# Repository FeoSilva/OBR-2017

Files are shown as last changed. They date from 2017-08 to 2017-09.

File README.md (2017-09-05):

# OBR 2017 - Equipe Robonáticos
Robô autônomo (Paulo) participante da Olimpíada Brasileira de Robótica.
<br><br>
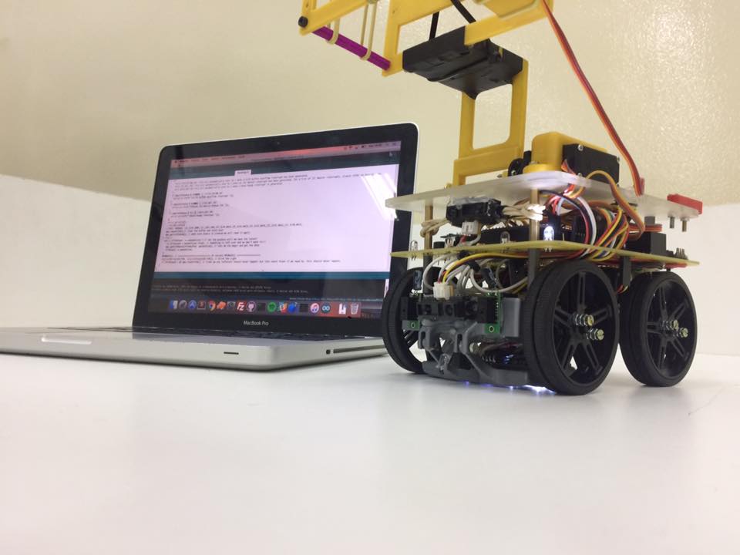
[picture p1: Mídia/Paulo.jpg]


Competições:
- Etapa Regional (FEI I) - 11/08/2017 - 1° lugar com 490 pts na somatória
- Etapa Estadual (FEI) - 09/09/2017

Resultados da Etapa Regional:
http://www.sistemaolimpo.org/regionais/results.php?eventID=3

<b>Divisões</b>
- Mecânica (12 versões do robô feitas para etapa regional utilizando o SolidWorks)
- Eletrônica (3 versões da Placa Principal para etapa regional utilizando o Eagle)
- Programação (45 versões do código até o final - Código em C++)

<b>Componentes do robô:</b><br>
<a href="https://store.arduino.cc/usa/arduino-mega-2560-rev3">- 1x Arduino Mega</a><br>
<a href="https://www.pololu.com/product/3045">- 4x 298:1 Micro Metal Gearmotor HPCB 12V</a><br>
<a href="https://www.pololu.com/product/713/resources">- 1x TB6612FNG (Controlador dos Motores);</a><br>
<a href="https://www.pololu.com/product/1425">- 8x Rodas Pololu 70x8mm</a><br>
<a href="https://www.filipeflop.com/produto/acelerometro-e-giroscopio-3-eixos-6-dof-mpu-6050/">- 1x MPU6050 - Acelerômetro e Giroscópio</a><br>
<a href="https://www.pololu.com/product/1134">- 4x Sharp Sensor Digital 2-10 cm</a><br>
<a href="https://www.pololu.com/product/2464">- 2x Sharp Sensor Analógico 4-30 cm</a><br>
<a href="https://www.pololu.com/product/960">- 1x QTR Sensor Array Analógico</a><br>
<a href="http://www.usinainfo.com.br/sensores-para-arduino/sensor-de-cor-para-arduino-tcs230-2810.html">- 2x TSC 230 - Sensor de Cor</a><br>
<a href="http://produto.mercadolivre.com.br/MLB-876602966-bateria-lipo-turnigy-2200mah-3s-111v-20c-_JM">- 1x Bateria de Li-po 11.1V 3S</a><br>
<a href="https://www.filipeflop.com/produto/servo-towerpro-mg995-metalico/">- 1x Servo MG995 15 kg.F.cm</a><br>
<a href="https://www.filipeflop.com/produto/micro-servo-9g-sg90-towerpro/">- 1x Micro servo SG90 Tower Pro</a>

<b>Fatores que serão melhorados/implementados para Etapa Estadual</b>
- Inclusão de encoder nos motores para aperfeiçoar as verificações e curvas do robô<br>
- Replanejamento dos sensores de distância para identificar as vítimas<br>
- Aperfeiçoamento da mecânica geral do robô para melhorar o centro de massa e diminuir sua altura<br>
- Aperfeiçoamento do mecanismo de recolher as vitímas<br>
- Implementação do algoritmo de cálculo percentual de proximidade de cor para detectar melhor a fita verde

<b>Integrantes:</b>
- Felipe Oliveira Silva (18 anos - Programação / Eletrônica);
- Antonio Pereira de Lima Neto (18 anos - Programação);
- Giovanna Ferreira Diodato (16 anos - Programação);
- Felipe de Souza Tiozo (17 anos - Mecânica / Eletrônica);

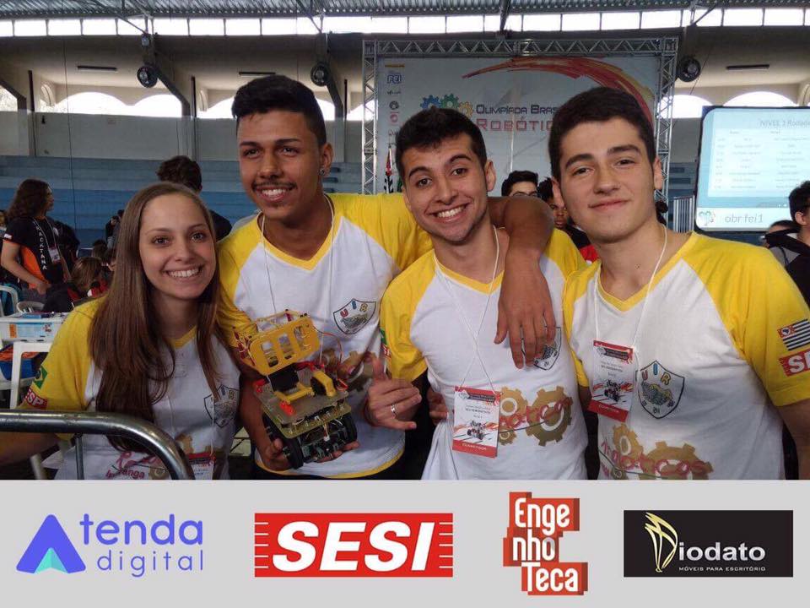
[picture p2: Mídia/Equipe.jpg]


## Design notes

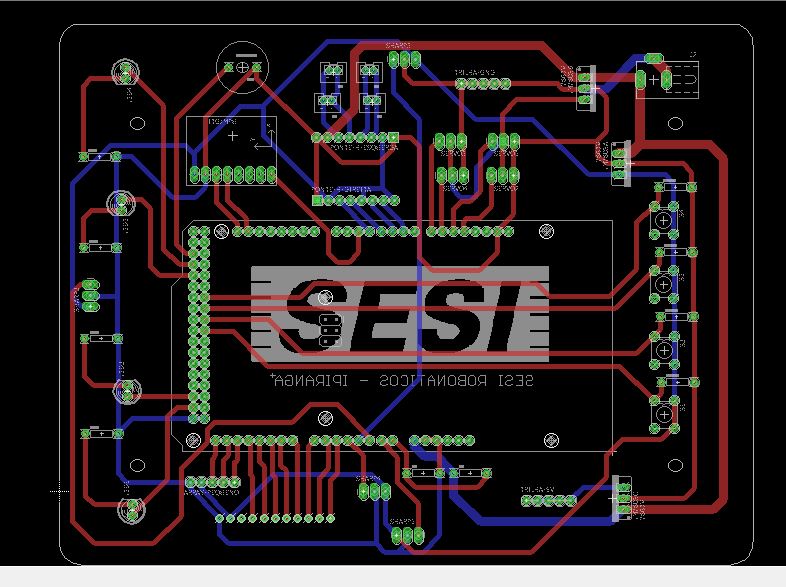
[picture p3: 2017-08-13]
Eletrônica/Paulo V2/placa.JPG

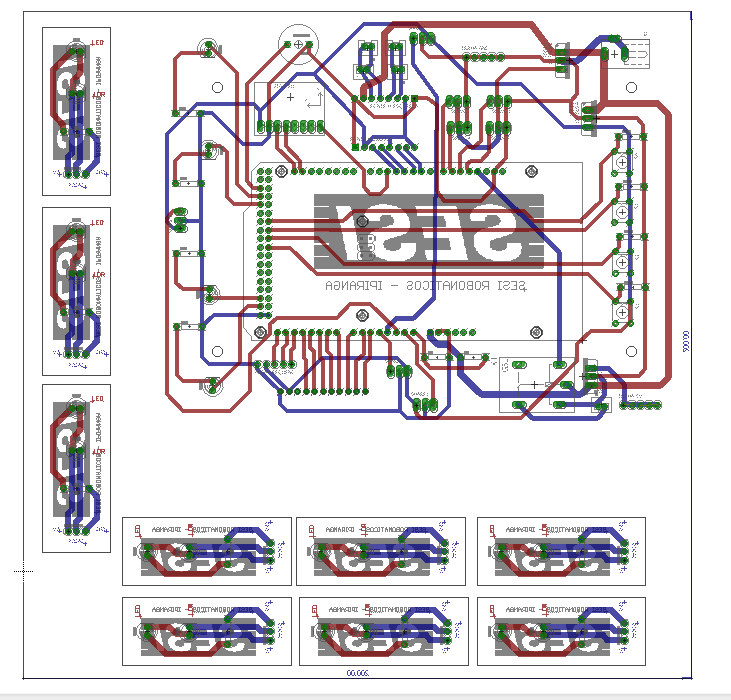
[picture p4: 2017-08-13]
Eletrônica/Placa Final/placa-final.PNG

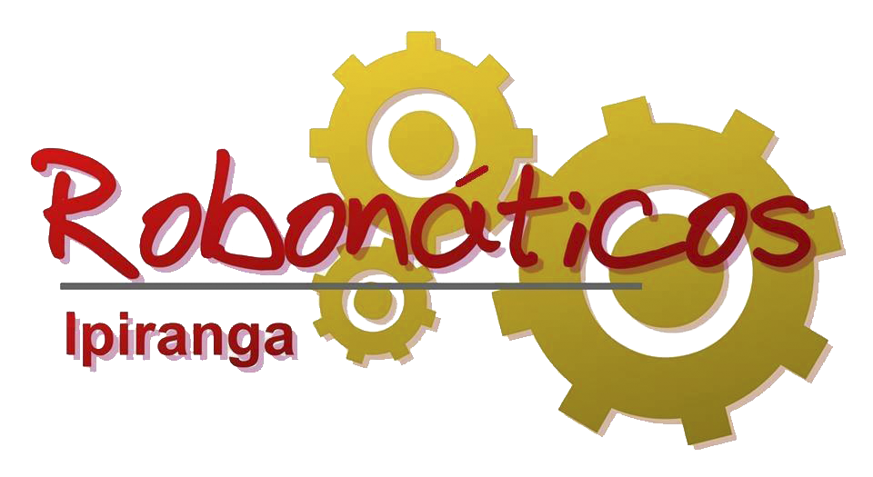
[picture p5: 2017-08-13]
Eletrônica/Placa LDR/robonaticos.png

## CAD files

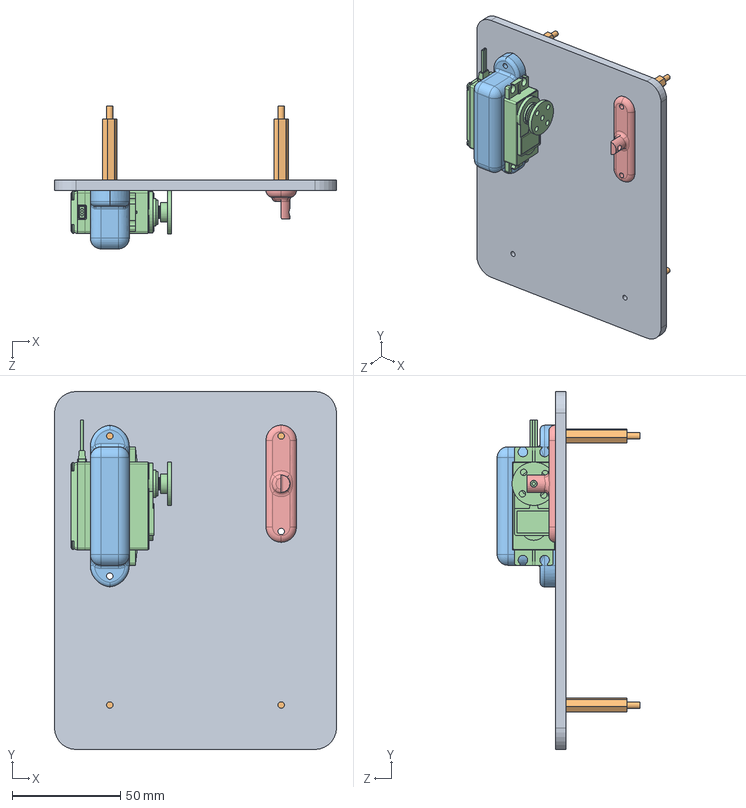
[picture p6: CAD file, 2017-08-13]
Mecânica/Paulo V12/Garra/Garra.SLDASM
130.0 x 165.0 x 65.8 mm
Chassi-Cima
Standoff-Nylon x 4
Suporte-Servo-MG
Servo-MG-995
Mancal

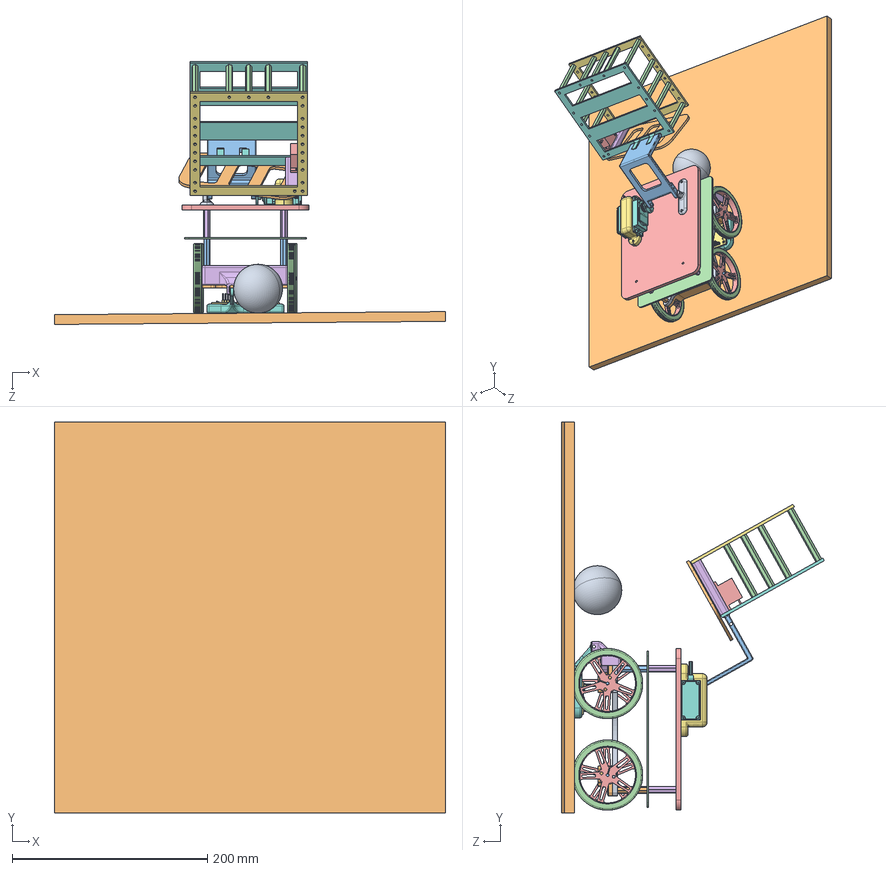
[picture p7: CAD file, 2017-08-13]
Mecânica/Paulo V12/Paulo-Montagem.SLDASM
400.1 x 400.0 x 269.0 mm
Chassi-Baixo
Suporte-Motor x 2
Pololu #2218 Micro Metal Gearmotor HP x 4
Borracha x 4
Roda x 4
Suporte-Trava-Array
Color_sensor x 2
Suporte-Array-Movel (1)
Standoff-Baixo-Maior x 2
Standoff-Baixo-Menor x 2
PCB
Chassi-Cima
Standoff-Nylon x 4
Suporte-Servo-MG
Servo-MG-995
Mancal
Piso
Mecanismo
Standoff-Garra x 12
Servo-9g
Suporte-Servo-Caixa
Base-Caixa
Tampa-Caixa
Vitima
Porta-Servo

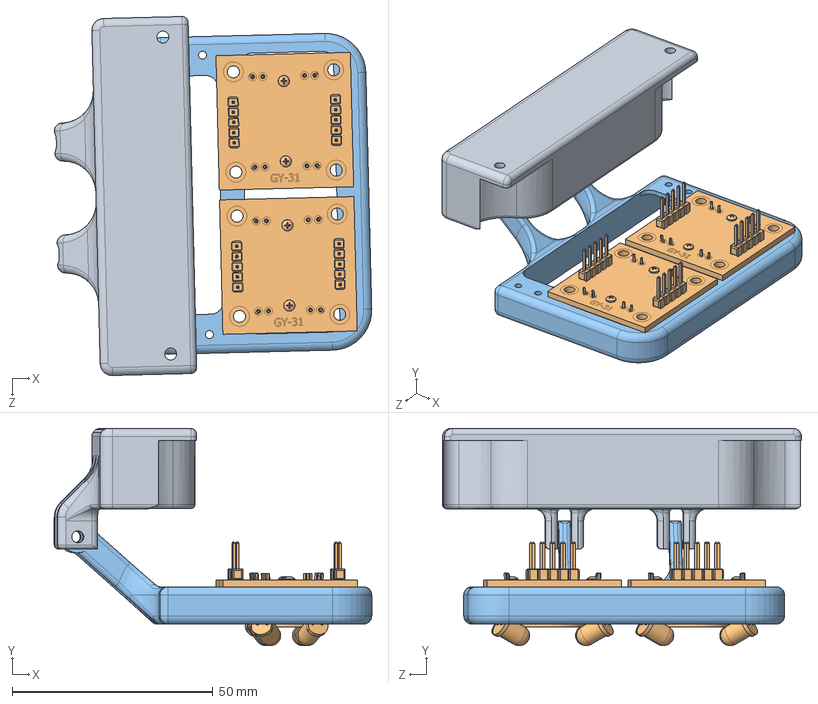
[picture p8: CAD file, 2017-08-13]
Mecânica/Paulo V12/Suporte-Array/Montagem-Suporte-Sensor.SLDASM
79.1 x 54.1 x 89.5 mm
Suporte-Trava-Array
Color_sensor x 2
Suporte-Array-Movel (1)

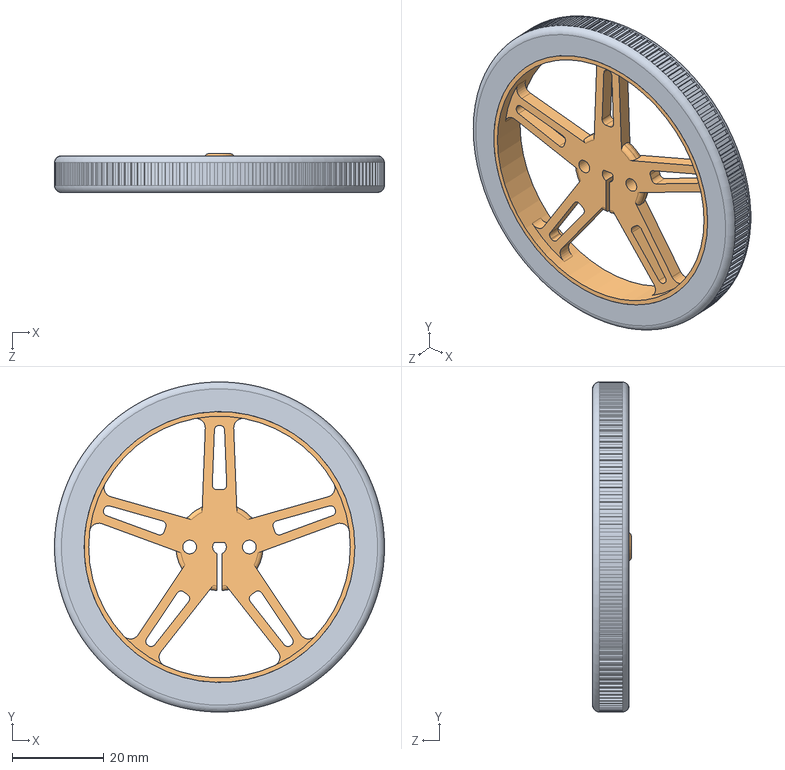
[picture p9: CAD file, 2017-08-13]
Mecânica/Paulo V12/Mobilidade/Pneu/Pneu.SLDASM
71.9 x 71.9 x 8.50 mm
Borracha
Roda

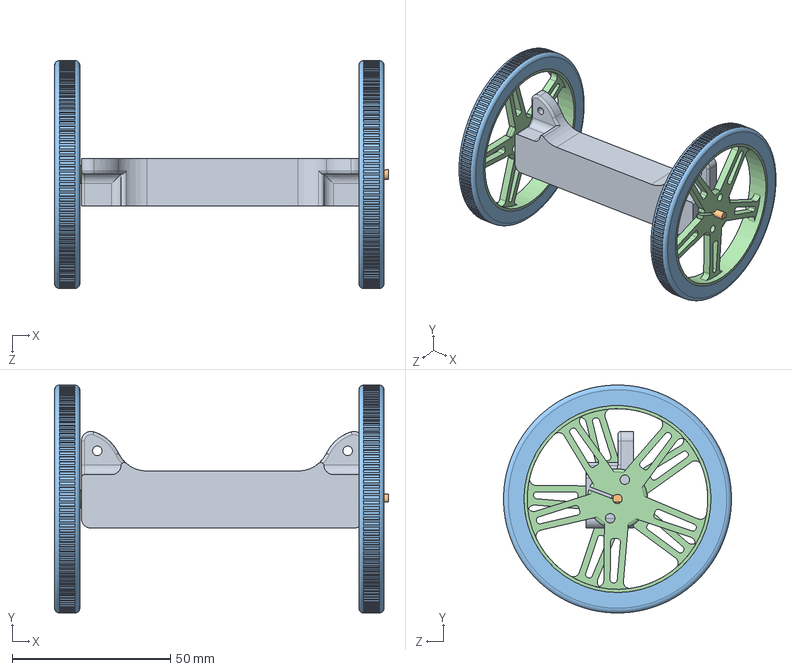
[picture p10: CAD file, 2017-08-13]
Mecânica/Paulo V12/Mobilidade/Motores-Suporte-Roda.SLDASM
105.4 x 71.9 x 71.9 mm
Suporte-Motor
Pololu #2218 Micro Metal Gearmotor HP x 2
Borracha x 2
Roda x 2

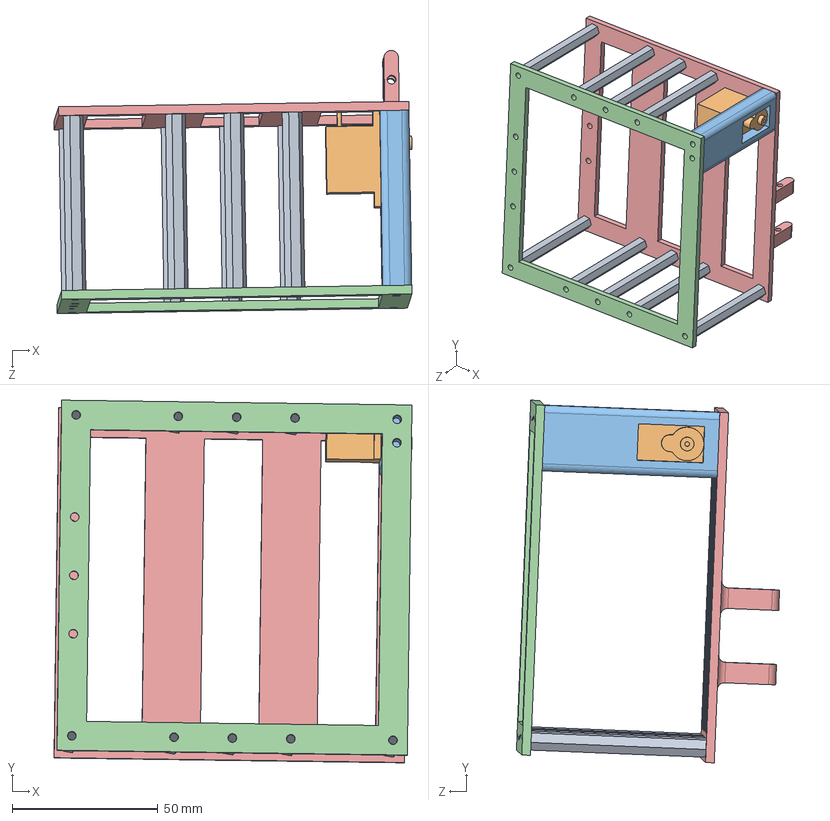
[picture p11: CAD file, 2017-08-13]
Mecânica/Paulo V12/Garra/Armazenamento/Caixa.SLDASM
122.6 x 124.2 x 90.1 mm
Standoff-Garra x 9
Servo-9g
Suporte-Servo-Caixa
Base-Caixa
Tampa-Caixa

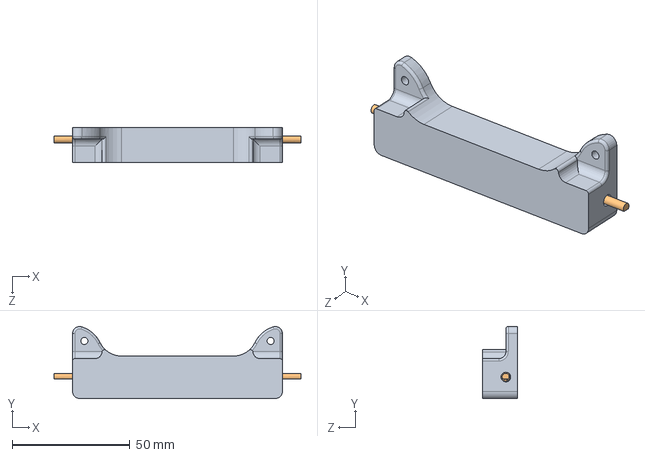
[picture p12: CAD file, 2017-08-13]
Mecânica/Paulo V12/Mobilidade/Suporte-Motor/Motores-Com-Suporte.SLDASM
104.7 x 30.5 x 15.0 mm
Suporte-Motor
Pololu #2218 Micro Metal Gearmotor HP x 2

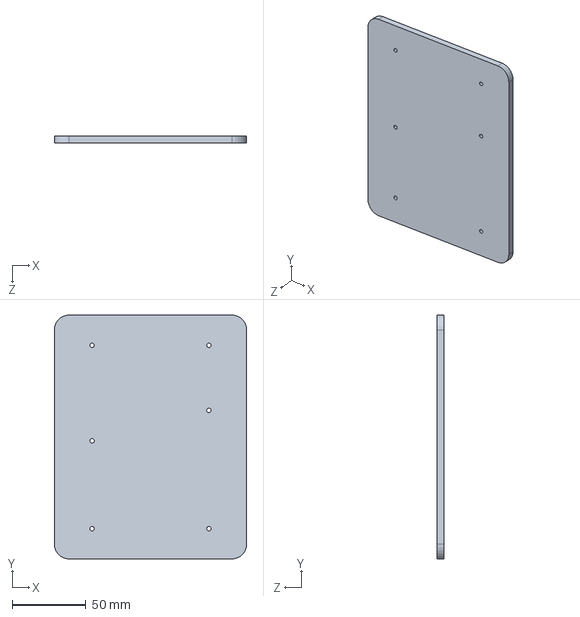
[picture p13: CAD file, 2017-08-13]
Mecânica/Paulo V12/Chassi-Cima/Chassi-Cima.SLDPRT
130.0 x 165.0 x 5.00 mm

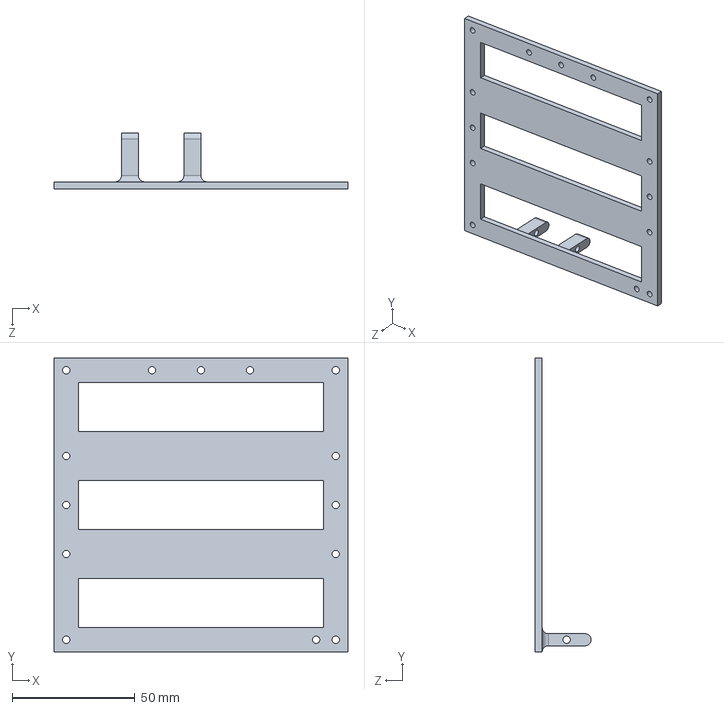
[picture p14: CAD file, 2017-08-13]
Mecânica/Paulo V12/Garra/Armazenamento/Tampa-Caixa.SLDPRT
120.0 x 120.0 x 23.0 mm

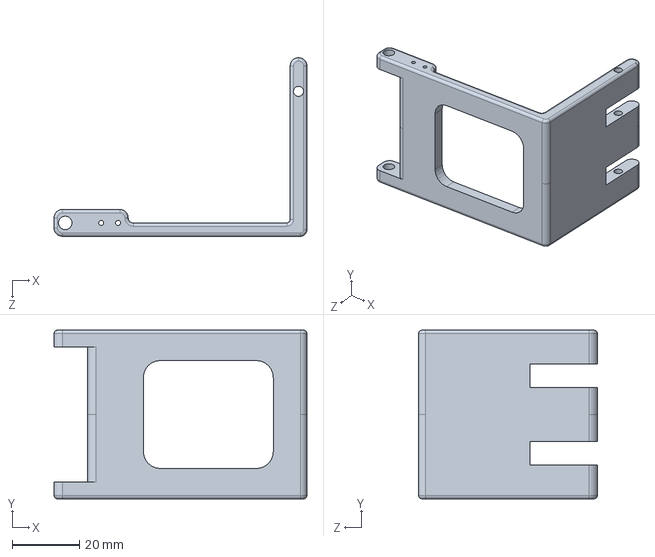
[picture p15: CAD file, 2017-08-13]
Mecânica/Paulo V12/Garra/Mecanismo/Mecanismo.SLDPRT
75.0 x 50.0 x 53.0 mm

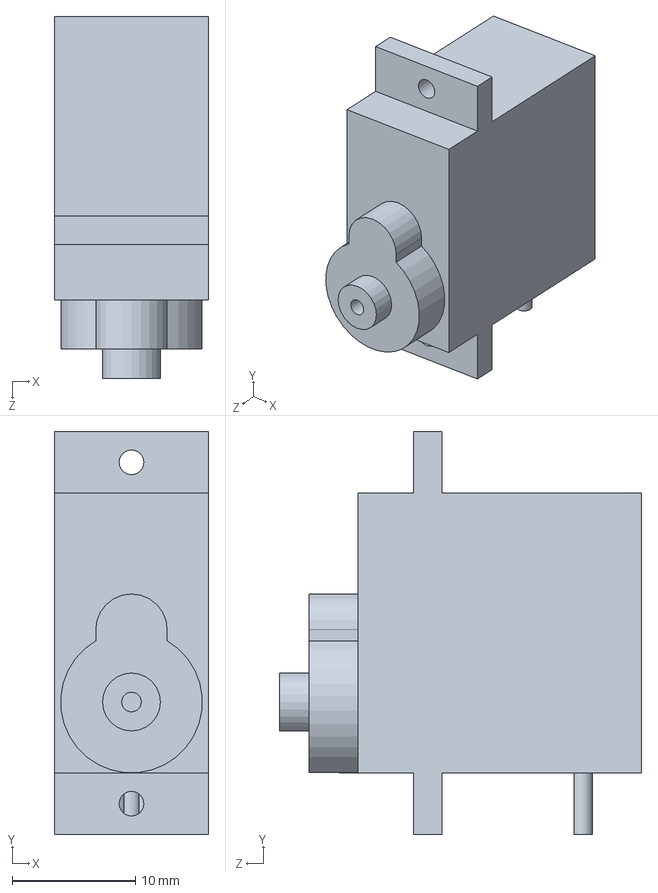
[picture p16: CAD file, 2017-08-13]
Mecânica/Paulo V12/Garra/Servos/Servo-9g.SLDPRT
12.5 x 32.7 x 29.4 mm

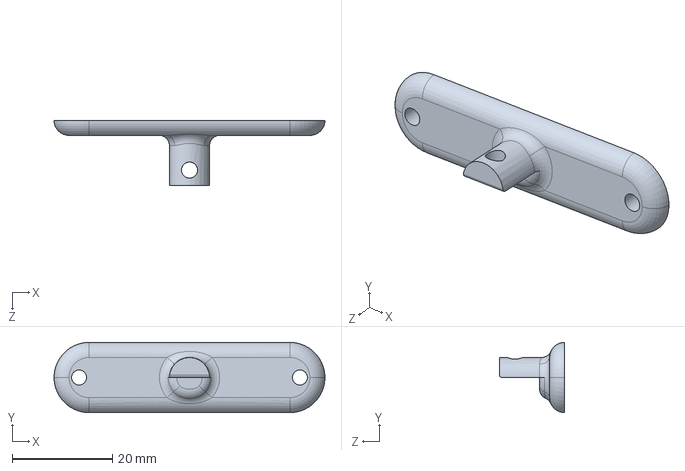
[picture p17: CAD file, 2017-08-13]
Mecânica/Paulo V12/Garra/Suporte-Servo/Mancal.SLDPRT
54.0 x 14.0 x 13.0 mm

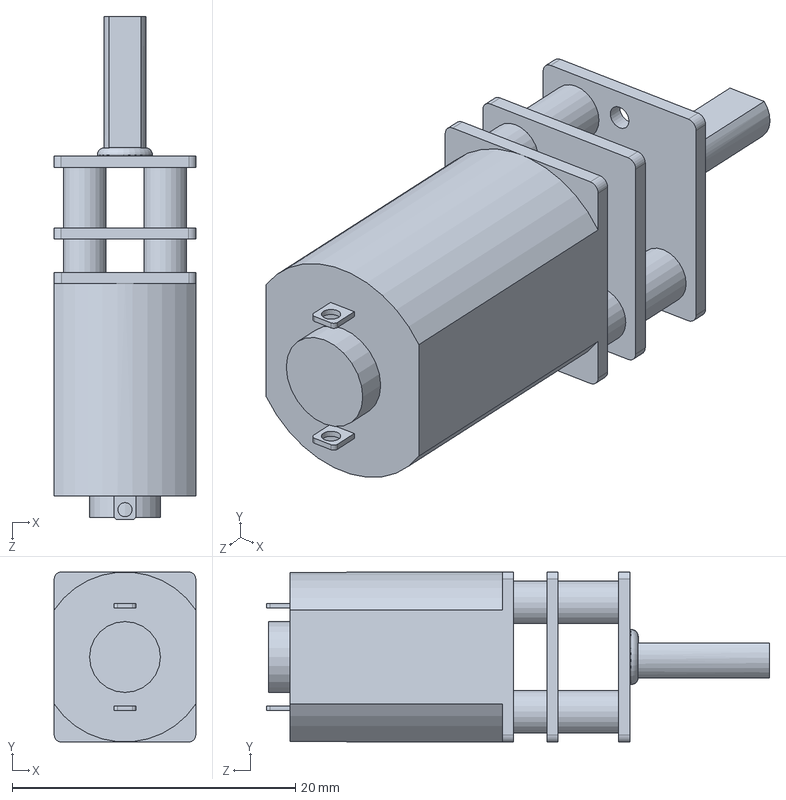
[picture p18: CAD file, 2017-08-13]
Mecânica/Paulo V12/Mobilidade/Suporte-Motor/Pololu #2218 Micro Metal Gearmotor HP.SLDPRT
10.0 x 12.0 x 35.5 mm

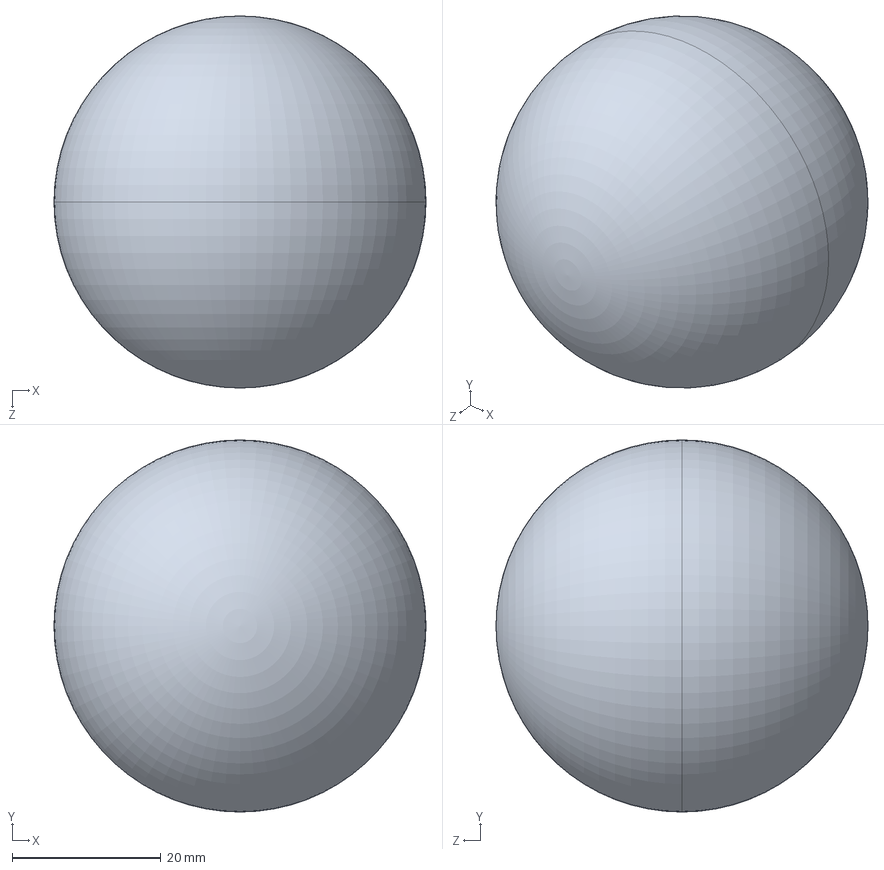
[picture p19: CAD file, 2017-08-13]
Mecânica/Paulo V12/Objetos/Vitima.SLDPRT
50.0 x 50.0 x 50.0 mm

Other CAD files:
Mecânica/Paulo V12/Sensores/Arduino Mega 2560.SLDPRT
Mecânica/Paulo V12/Standoff/Standoff-Nylon.SLDPRT
Mecânica/Paulo V12/Chassi-Baixo/Chassi-Baixo.SLDPRT
Mecânica/Paulo V12/Garra/Armazenamento/Porta-Servo.SLDPRT
Mecânica/Paulo V1/Chassi cima.SLDPRT
Mecânica/Paulo V1/MicroMotor.SLDPRT
Mecânica/Paulo V1/Montagem1.SLDASM
Mecânica/Paulo V1/PCB.SLDPRT
Mecânica/Paulo V1/PCB2.SLDPRT
Mecânica/Paulo V1/Pololu #2218 Micro Metal Gearmotor HP.SLDPRT
Mecânica/Paulo V1/Suporte array teste.SLDPRT
Mecânica/Paulo V1/Suporte array.SLDPRT
Mecânica/Paulo V1/chassi.SLDPRT
Mecânica/Paulo V1/standoff maior.SLDPRT
Mecânica/Paulo V1/standoff menor.SLDPRT
Mecânica/Paulo V1/standoff.SLDPRT
Mecânica/Paulo V1/standoff2.SLDPRT
Mecânica/Paulo V1/suporte motor.SLDPRT
Mecânica/Paulo V1/suporte sharp.SLDPRT
Mecânica/Paulo V1/supp.SLDPRT
Mecânica/Paulo V1/supp2.SLDPRT
Mecânica/Paulo V1/supp3.SLDPRT
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

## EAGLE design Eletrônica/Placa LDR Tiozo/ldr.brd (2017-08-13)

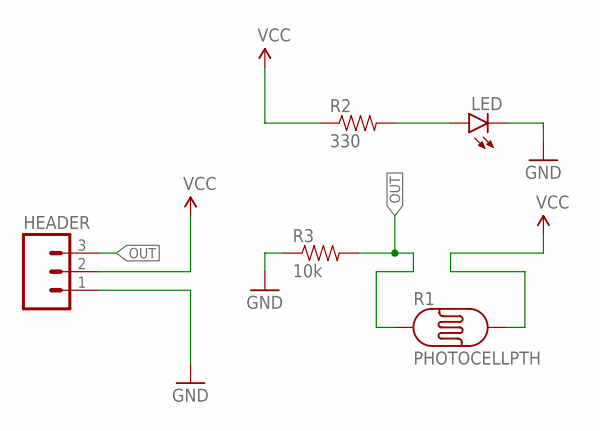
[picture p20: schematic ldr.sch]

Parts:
HEADER: M03PTH; 1X03
LED: LED5MM
R1: PHOTOCELLPTH; PHOTOCELL
R2: 330; AXIAL-0.3EZ
R3: 10k; AXIAL-0.3EZ

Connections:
GND: HEADER.1, LED.K (C), R3.P$1 (1)
unnamed: LED.A, R2.P$2 (2)
OUT: HEADER.3, R1.1, R3.P$2 (2)
VCC: HEADER.2, R1.2, R2.P$1 (1)

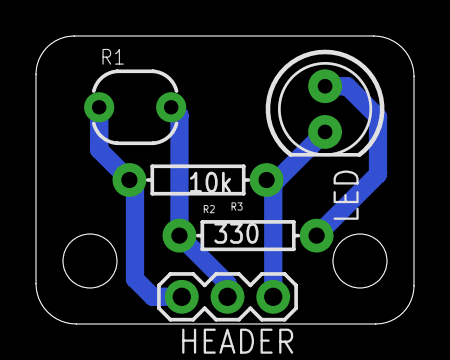
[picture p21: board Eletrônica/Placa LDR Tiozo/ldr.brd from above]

Board: 2 copper layers, 21.0 x 16.0 mm, 5 parts (0 on the bottom side), 4 nets.

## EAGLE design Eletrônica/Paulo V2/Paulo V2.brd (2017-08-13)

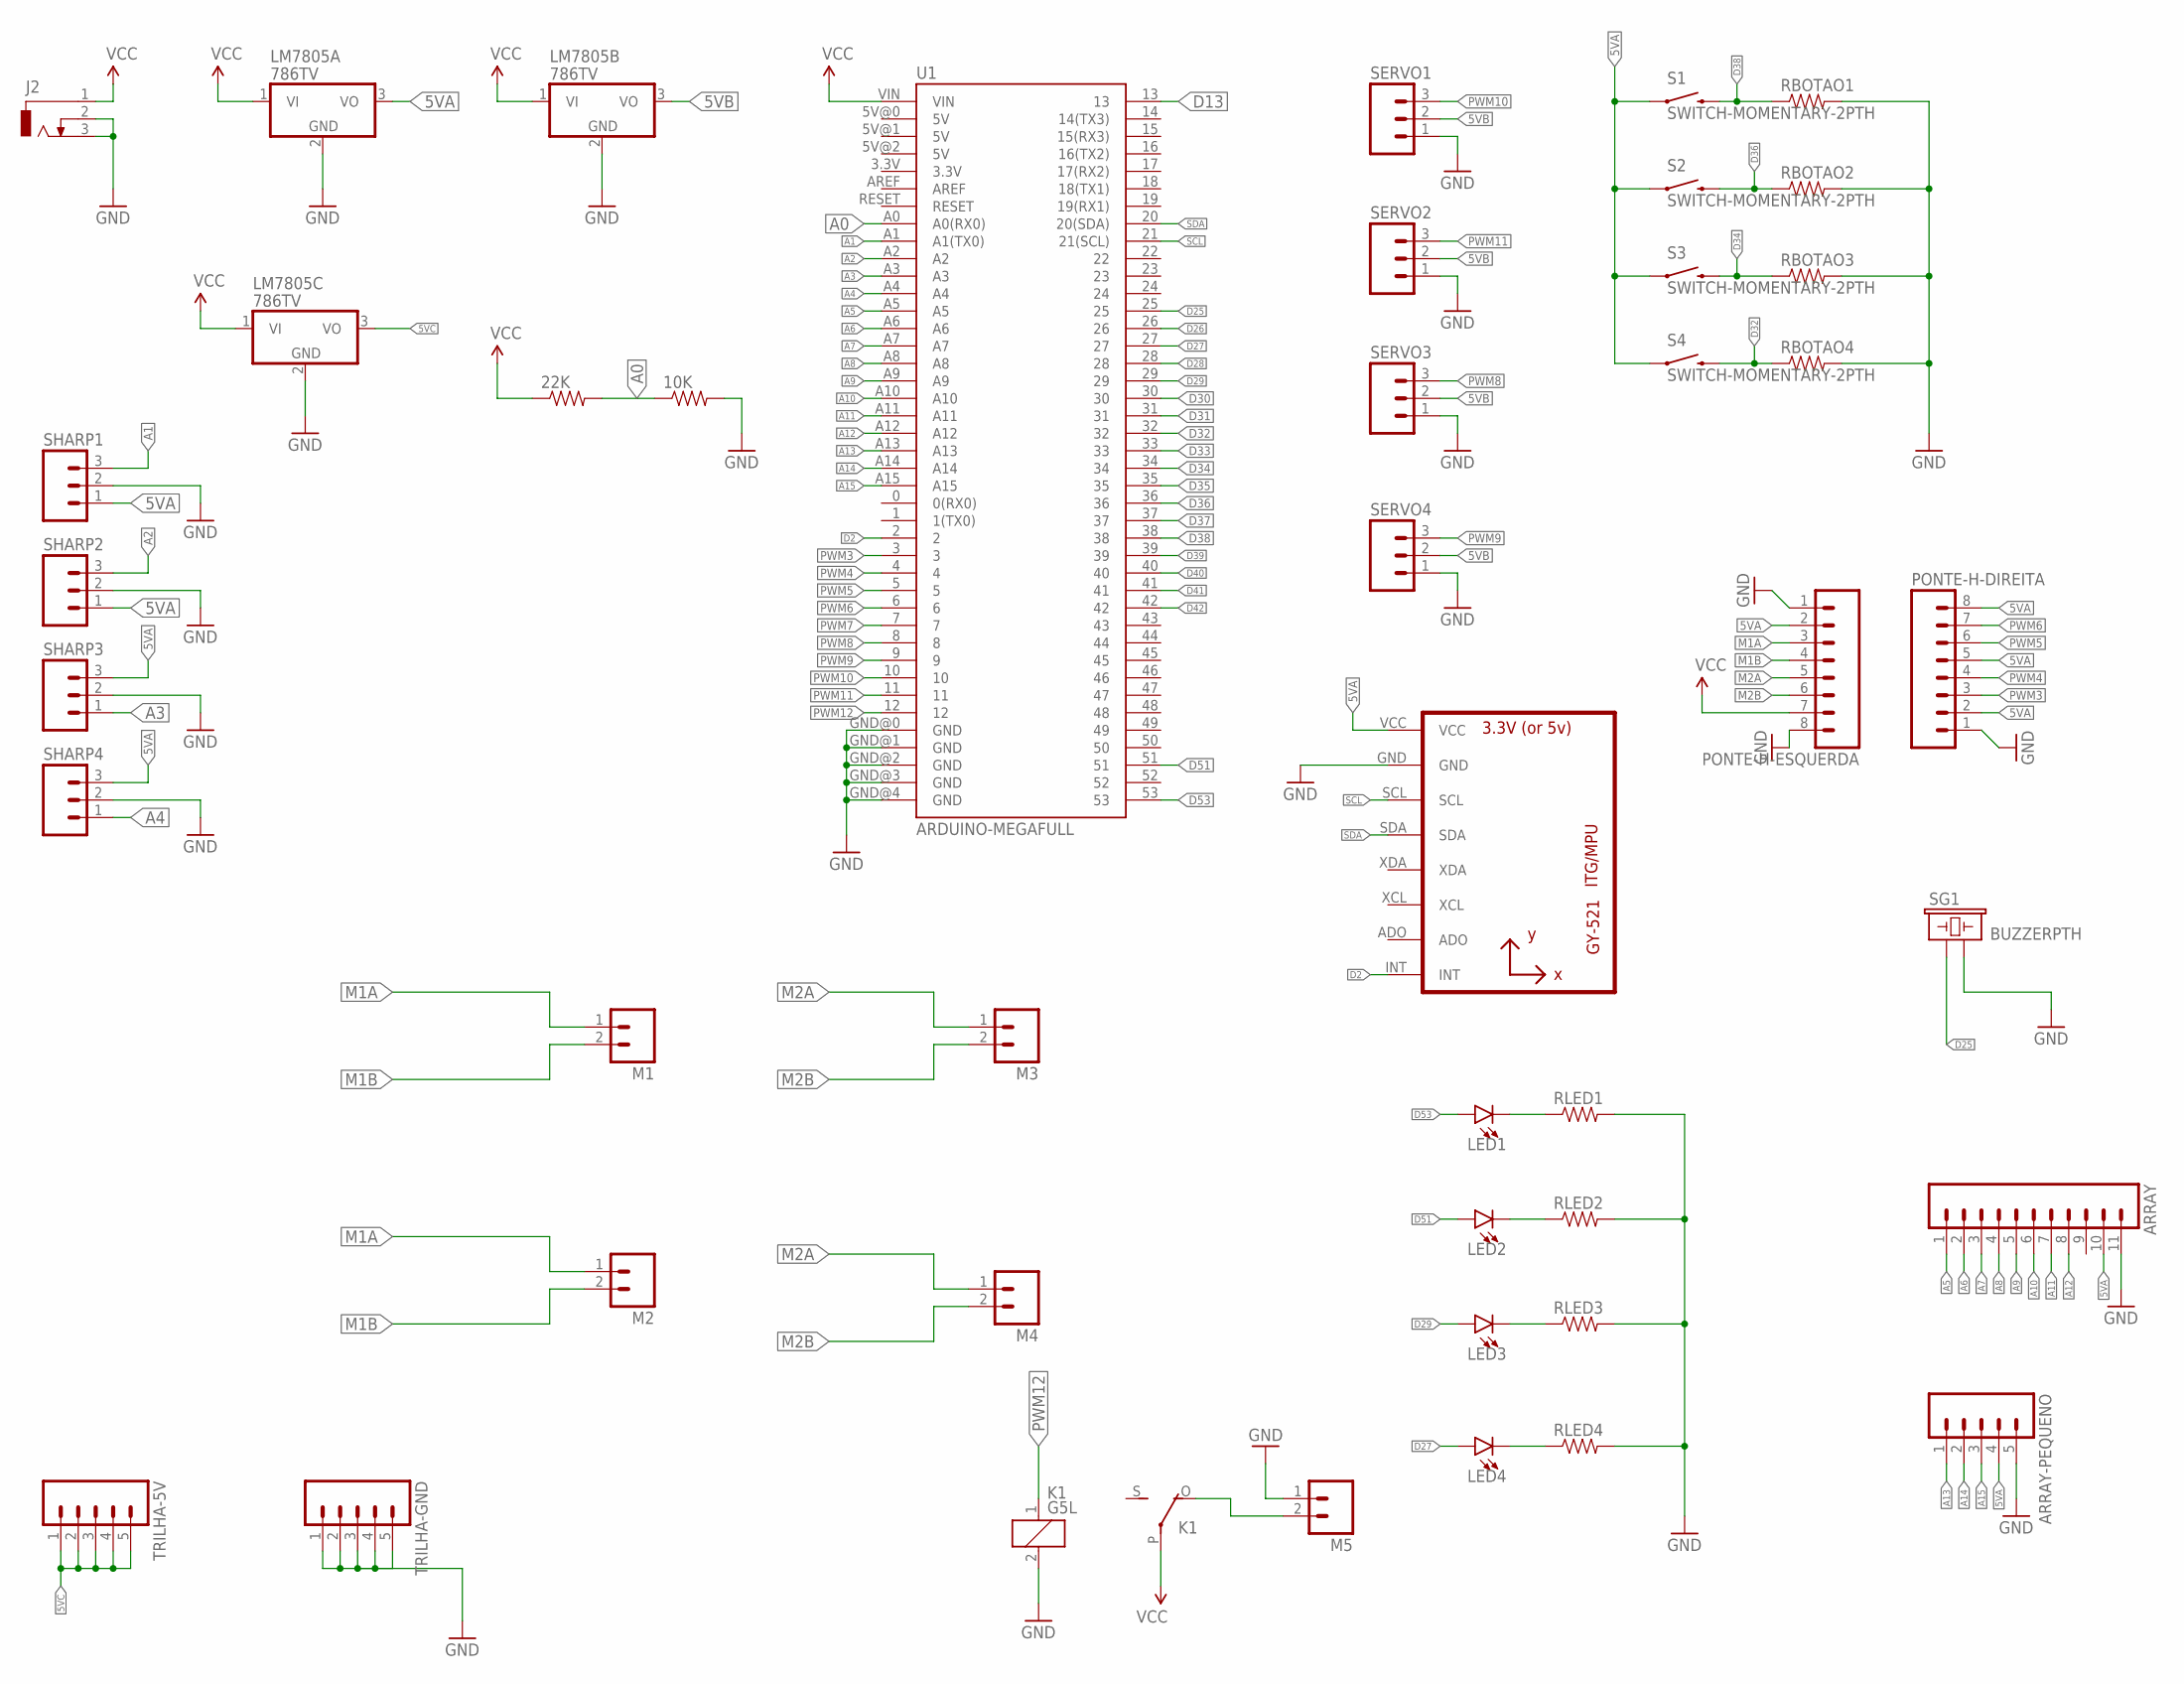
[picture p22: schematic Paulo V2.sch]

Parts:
10K, 22K: RESISTOREZ; AXIAL-0.3EZ
ARRAY: M11POGOPIN_HOLES_ONLY; 1X11_HOLES_ONLY
ARRAY-PEQUENO: M05PTH; 1X05
J2: DCJ0303
K1: G5L; G5LE
LED1, LED2, LED3, LED4: LED5MM; LED_5MM
LM7805A, LM7805B, LM7805C: 786TV; TO220V
M1, M2, M3, M4, M5: M02JST-PTH-VERT; JST-2-PTH-VERT
PONTE-H-DIREITA: M08NO_SILK; 1X08_PIN1_NO_SILK
PONTE-H-ESQUERDA: M08NO_SILK; 1X08_PIN1_NO_SILK
RBOTAO1, RBOTAO2, RBOTAO3, RBOTAO4: RESISTOREZ; AXIAL-0.3EZ
RLED1, RLED2, RLED3, RLED4: RESISTOREZ; AXIAL-0.3EZ
S1, S2, S3, S4: SWITCH-MOMENTARY-2PTH; TACTILE-PTH
SERVO1, SERVO2, SERVO3, SERVO4: M03LONGPADS; 1X03_LONGPADS@1
SG1: BUZZERPTH; BUZZER-12MM
SHARP1, SHARP2, SHARP3, SHARP4: M03LONGPADS; 1X03_LONGPADS@1
TRILHA-5V: M05PTH; 1X05
TRILHA-GND: M05PTH; 1X05
U1: ARDUINO-MEGAFULL; ARDUINO_MEGA
U2: GY-521MPU6050; GY-521

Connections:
5VA: ARRAY.10, ARRAY-PEQUENO.4, LM7805A.3 (VO), PONTE-H-DIREITA.2, PONTE-H-DIREITA.5, PONTE-H-DIREITA.8, PONTE-H-ESQUERDA.2, S1.1, S2.1, S3.1, S4.1, SHARP1.1, SHARP2.1, SHARP3.3, SHARP4.3, U2.VCC
5VB: LM7805B.3 (VO), SERVO1.2, SERVO2.2, SERVO3.2, SERVO4.2
5VC: LM7805C.3 (VO), TRILHA-5V.1, TRILHA-5V.2, TRILHA-5V.3, TRILHA-5V.4, TRILHA-5V.5
A0: 10K.P$1 (1), 22K.P$2 (2), U1.A0 (A0(RX0))
A1: SHARP1.3, U1.A1 (A1(TX0))
A2: SHARP2.3, U1.A2
A3: SHARP3.1, U1.A3
A4: SHARP4.1, U1.A4
A5: ARRAY.1, U1.A5
A6: ARRAY.2, U1.A6
A7: ARRAY.3, U1.A7
A8: ARRAY.4, U1.A8
A9: ARRAY.5, U1.A9
A10: ARRAY.6, U1.A10
A11: ARRAY.7, U1.A11
A12: ARRAY.8, U1.A12
A13: ARRAY-PEQUENO.1, U1.A13
A14: ARRAY-PEQUENO.2, U1.A14
A15: ARRAY-PEQUENO.3, U1.A15
D2: U1.2, U2.INT
D13: U1.13
D25: SG1.+ (1), U1.25
D26: U1.26
D27: LED4.A, U1.27
D28: U1.28
D29: LED3.A, U1.29
D30: U1.30
D31: U1.31
D32: RBOTAO4.P$1 (1), S4.3 (2), U1.32
D33: U1.33
D34: RBOTAO3.P$1 (1), S3.3 (2), U1.34
D35: U1.35
D36: RBOTAO2.P$1 (1), S2.3 (2), U1.36
D37: U1.37
D38: RBOTAO1.P$1 (1), S1.3 (2), U1.38
D39: U1.39
D40: U1.40
D41: U1.41
D42: U1.42
D51: LED2.A, U1.51
D53: LED1.A, U1.53
GND: 10K.P$2 (2), ARRAY.11, ARRAY-PEQUENO.5, J2.2, J2.3, K1.2, LM7805A.2 (GND), LM7805B.2 (GND), LM7805C.2 (GND), M5.1, PONTE-H-DIREITA.1, PONTE-H-ESQUERDA.1, PONTE-H-ESQUERDA.8, RBOTAO1.P$2 (2), RBOTAO2.P$2 (2), RBOTAO3.P$2 (2), RBOTAO4.P$2 (2), RLED1.P$2 (2), RLED2.P$2 (2), RLED3.P$2 (2), RLED4.P$2 (2), SERVO1.1, SERVO2.1, SERVO3.1, SERVO4.1, SG1.- (2), SHARP1.2, SHARP2.2, SHARP3.2, SHARP4.2, TRILHA-GND.1, TRILHA-GND.2, TRILHA-GND.3, TRILHA-GND.4, TRILHA-GND.5, U1.GND@0 (GND), U1.GND@1 (GND), U1.GND@2 (GND), U1.GND@3 (GND), U1.GND@4 (GND), U2.GND
M1A: M1.1, M2.1, PONTE-H-ESQUERDA.3
M1B: M1.2, M2.2, PONTE-H-ESQUERDA.4
M2A: M3.1, M4.1, PONTE-H-ESQUERDA.5
M2B: M3.2, M4.2, PONTE-H-ESQUERDA.6
unnamed: LED1.K (C), RLED1.P$1 (1)
unnamed: LED2.K (C), RLED2.P$1 (1)
unnamed: LED3.K (C), RLED3.P$1 (1)
unnamed: LED4.K (C), RLED4.P$1 (1)
unnamed: K1.O, M5.2
PWM3: PONTE-H-DIREITA.3, U1.3
PWM4: PONTE-H-DIREITA.4, U1.4
PWM5: PONTE-H-DIREITA.6, U1.5
PWM6: PONTE-H-DIREITA.7, U1.6
PWM7: U1.7
PWM8: SERVO3.3, U1.8
PWM9: SERVO4.3, U1.9
PWM10: SERVO1.3, U1.10
PWM11: SERVO2.3, U1.11
PWM12: K1.1, U1.12
SCL: U1.21 (21(SCL)), U2.SCL
SDA: U1.20 (20(SDA)), U2.SDA
VCC: 22K.P$1 (1), J2.1, K1.P, LM7805A.1 (VI), LM7805B.1 (VI), LM7805C.1 (VI), PONTE-H-ESQUERDA.7, U1.VIN

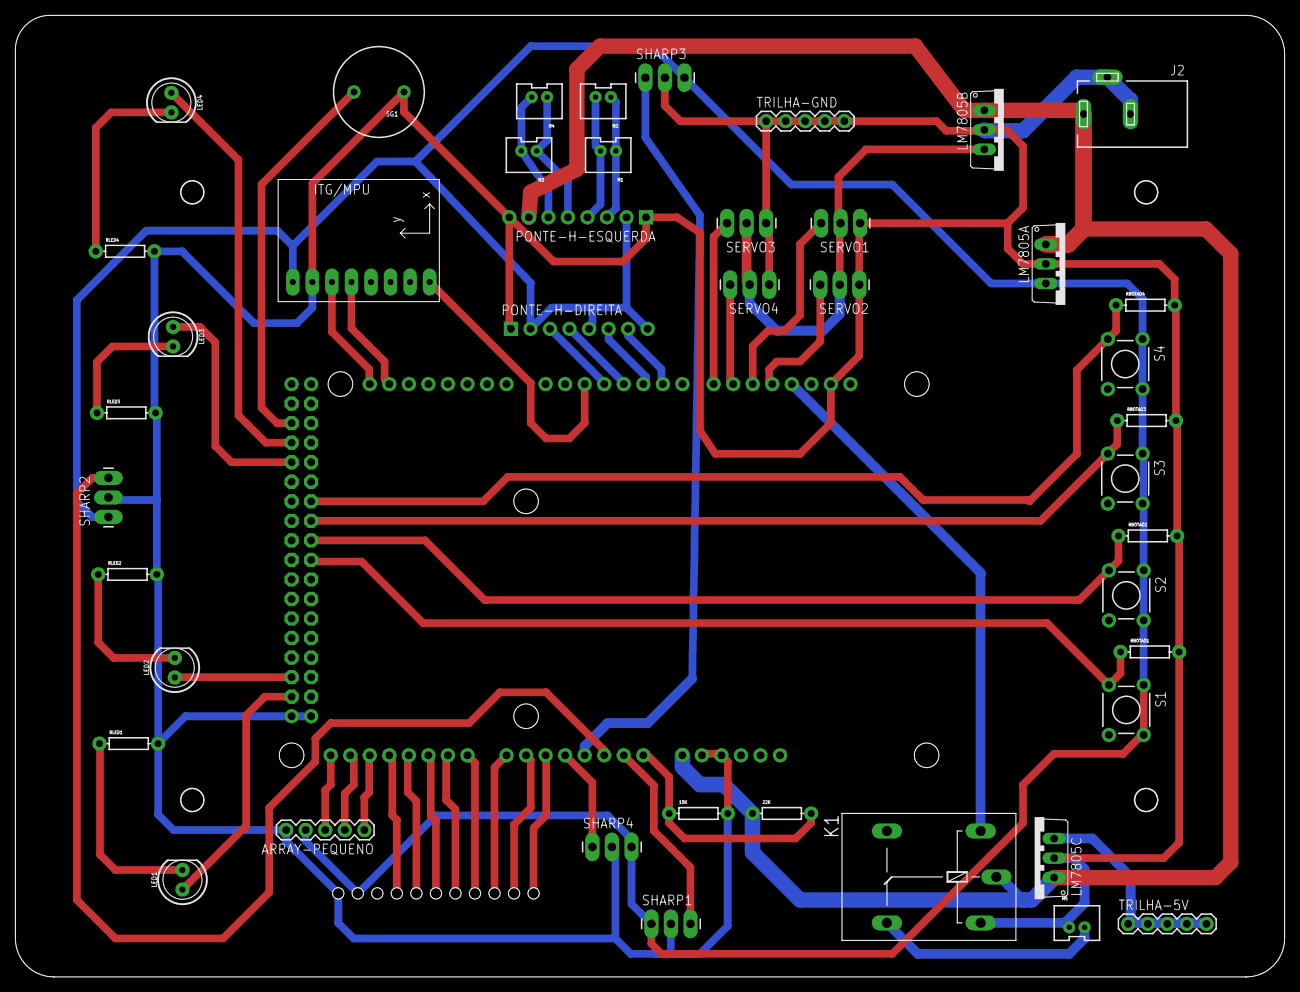
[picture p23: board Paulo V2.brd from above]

Board: 2 copper layers, 165.0 x 125.0 mm, 45 parts (1 on the bottom side), 51 nets.

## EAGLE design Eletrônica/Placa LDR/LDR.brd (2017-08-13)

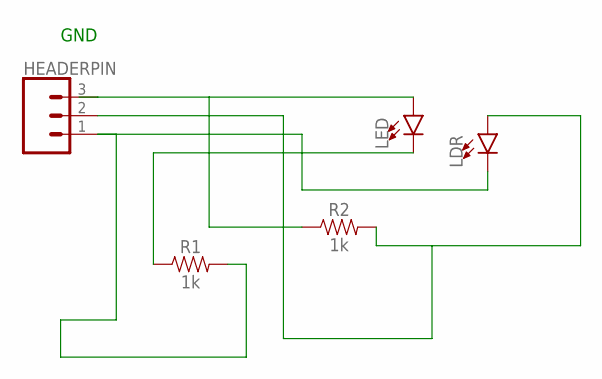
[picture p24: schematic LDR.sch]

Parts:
HEADERPIN: CONN_03; 1X03
LDR: LED5MM; LED_5MM
LED: LED5MM; LED_5MM
R1, R2: 1k; AXIAL-0.3

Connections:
unnamed: HEADERPIN.3, LED.A, R2.P$1 (1)
unnamed: LED.K (C), R1.P$1 (1)
unnamed: HEADERPIN.1, LDR.K (C), R1.P$2 (2)
unnamed: HEADERPIN.2, LDR.A, R2.P$2 (2)

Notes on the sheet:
GND

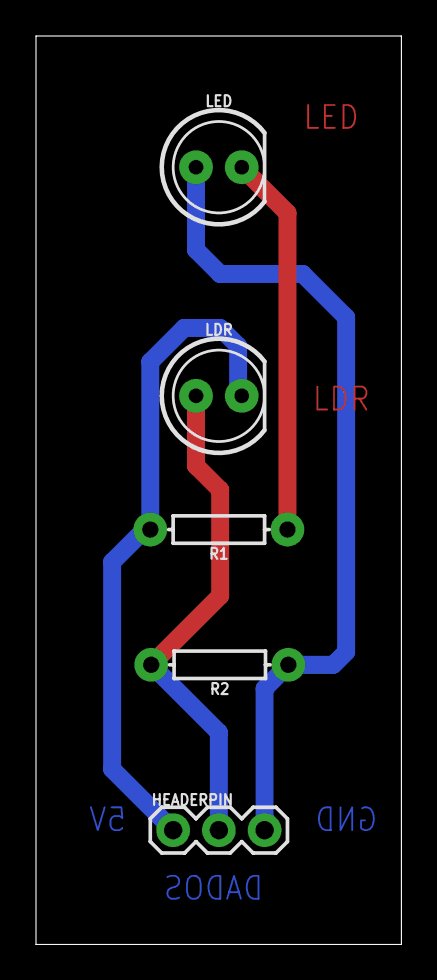
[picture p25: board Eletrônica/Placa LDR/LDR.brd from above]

Board: 2 copper layers, 20.3 x 50.5 mm, 5 parts (0 on the bottom side), 4 nets.

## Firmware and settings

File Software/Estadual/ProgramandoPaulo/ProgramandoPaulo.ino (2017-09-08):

/*
   Programacao para o torneio OBR 2017 - Etapa Estadual
   Desenvolvido por Felipe Silva, Felipe Tiozo, Antonio Pereira e Giovannna Diodato;
   Equipe Robonaticos;
   Apoio: Sesi São Paulo / Engenhoteca
   http://facebook.com/robonaticos
*/

#include <QTRSensors.h>
#include <Servo.h>

#include <Encoder.h>

// I2Cdev and MPU6050 must be installed as libraries, or else the .cpp/.h files
// for both classes must be in the include path of your project
#include "I2Cdev.h"

#include "Wire.h"
#include "MPU6050_6Axis_MotionApps20.h"
#include <Thread.h>
#include "AnalogIn.h"
#include "DigitalIn.h"
#include "DigitalOut.h"
#include <ArduinoSensors.h>
#include <sensors/AnalogVoltage.h>

/// Basic robot definitions
#include "Config.h"

#include "Readings.h" // lê
#include "Verifications.h" // verifica
#include "Actions.h" // age
#include "Controllers.h" // controla


void setup() {

  // i2c setup
  //Wire.begin();
  //TWBR = 24; // 400kHz I2C clock (200kHz if CPU is 8MHz)

  Serial.begin(115200);

  // SETUP DE TUDO
  ligarMotores(); // ligar motores
  debugEncoder();
  Servo1.attach(servo1);
  Servo1.write(93);
  Servo2.detach();
  Servo2.attach(servo2);
  Servo2.write(180);

  AlertaDeInicio();
  delay(500);


  Serial.println("Calibration Run");
  Serial.println("Calibration Running...");

  for (int i = 0; i < 100; i++)  // make the calibration take about 10 seconds
  {
    LED4.turnOn();
    qtra.calibrate();       // reads all sensors 10 times at 2500 us per read (i.e. ~25 ms per call)
    LED4.turnOff();
    delay(10);
  }

  LED4.turnOff();
  Serial.println("Calibration Done!");


  // Mostrar 'Inicializando...'
  Serial.println("Inicializando...");
  delay(800);

  Serial.println(F("Alive"));

  // put your setup code here, to run once:

  // MPU6050 init
  IMU_init();

}

void loop() {
  //Serial.println(getYPR(0));
  //MPU6050Connect();
  //lendoMpuGyro();
  lerTodosSensores(SHARPSensor);
  //mover(70, 70);
  //Seguidor(true);
  if (Botao1.readValue() == HIGH) {
    LED3.turnOn();
    delay(500);
    Rampa(true);
  }
  if (Botao2.readValue() == HIGH) {
    Resgate(true);
    //Verde(DIREITA);
    
    curvaEncoder(60, 100, ESQUERDA);
    //Curva90Graus(ESQUERDA, LIN);
  }
  if (Botao4.readValue() == HIGH) {
    resgate();
    //Curva90Graus(DIREITA, LIN);
  }
  
}

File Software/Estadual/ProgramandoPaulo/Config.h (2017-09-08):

#include <Arduino.h>

/*
  ROBOT GENERAL CONFIGURATION
*/

/************************ MOTORES ************************/
// Motores: Pololu 298:1 Micro Motor HPCB 12V 0.8A 100 RPM
// Utilizamos 4 motores porém eles estão em paralelo

// Motor ESQUERDO DIANETEIRO
#define MotorEsquerdoFrente 4
#define MotorEsquerdoTras 3

// Motor DIREITO DIANTEIRO

#define MotorDireitoFrente 6
#define MotorDireitoTras 5


void ligarMotores() {
  // MOTOR ESQUERDO DIANTEIRO
  pinMode(MotorEsquerdoFrente, OUTPUT);
  pinMode(MotorEsquerdoTras, OUTPUT);


  // MOTOR DIREITO DIANTEIRO
  pinMode(MotorDireitoFrente, OUTPUT);
  pinMode(MotorDireitoTras, OUTPUT);

}
// Encoder Motor Traseiro Esquerdo
// Change these two numbers to the pins connected to your encoder.
//   Best Performance: both pins have interrupt capability
//   Good Performance: only the first pin has interrupt capability
//   Low Performance:  neither pin has interrupt capability
#define encoderEsquerdoA 19
#define encoderEsquerdoB 18

Encoder encoderEsquerdo(encoderEsquerdoA, encoderEsquerdoB);


/************************ SENSORES ************************/
// Sensores: Pololu QTR-8A reflectance sensor, Sharp 4-30cm, Divisor de Tensão, GY521 IMU
// PORTAS ANÁLOGICAS

// SENSORES ARRAY QTR-8-A

#define luminosidade1     A5 // SENSOR LINHA 1
#define luminosidade2     A6 // SENSOR LINHA 2
#define luminosidade3     A7 // SENSOR LINHA 3
#define luminosidade4     A8 // SENSOR LINHA 4
#define luminosidade5     A9 // SENSOR LINHA 5
#define luminosidade6     A10 // SENSOR LINHA 6
#define luminosidade7     A11// SENSOR LINHA 7
#define luminosidade8     A12  // SENSOR LINHA 8

#define sensorVerdeEsquerda A13
#define sensorVerdeDireita A14

int QTR[] = {
  0,
  luminosidade1,
  luminosidade2,
  luminosidade3,
  luminosidade4,
  luminosidade5,
  luminosidade6,
  luminosidade7,
  luminosidade8,

};

// SETTINGS PARA LER O ARRAY COM A FUNÇÃO .readLine()
#define NUM_SENSORS             8  // number of sensors used
#define NUM_SAMPLES_PER_SENSOR  4  // average 4 analog samples per sensor reading
//#define EMITTER_PIN             2  // emitter is controlled by digital pin 2

// Sensores de 0 a 8 que estão conectados nas portas analógicas
QTRSensorsAnalog qtra((unsigned char[]) {
  luminosidade1, luminosidade2, luminosidade3, luminosidade4, luminosidade5, luminosidade6, luminosidade7, luminosidade8
},
NUM_SENSORS, NUM_SAMPLES_PER_SENSOR);
unsigned int sensorValues[NUM_SENSORS];


// SENSORES SHARP 4-30cm
#define sharp1     A4 // SENSOR ESQUERDA ok
#define sharp2     A2 // SENSOR FRENTE - CIMA
#define sharp3     A3 // SENSOR DIREITA OK
#define sharp4     A0 // SENSOR FRENTE - BAIXO OK
#define sharp5     A1 // SENSOR FRENTE - ESQUERDA ok
#define sharp6     A15 // SENSOR FRENTE - DIREITA

int Sharp[] {
  0,
  sharp1,
  sharp2,
  sharp3,
  sharp4,
  sharp5,
  sharp6
};



// Tensão Bateria
#define VBAT    A0 // SENSOR DE TENSÃO DA BATERIA
#define VOLTAGE_LOW   11.5 // Tensão mínima
#define VOLTAGE_HIGH  14 // Tensão maxima


// 0 in ADC now means -5v. full ADC (1024) means 10v
AnalogVoltage myCustomVoltimeter(VBAT, 0, 15.1);
// Turns LED on
float pinVoltage = myCustomVoltimeter.readVoltage();

// Giroscópio e AcelerometrO Gy 521
MPU6050 mpu;

// MPU control/status vars
bool dmpReady = false;  // set true if DMP init was successful
uint8_t mpuIntStatus;   // holds actual interrupt status byte from MPU
uint8_t devStatus;      // return status after each device operation (0 = success, !0 = error)
uint16_t packetSize;    // expected DMP packet size (default is 42 bytes)
uint16_t fifoCount;     // count of all bytes currently in FIFO
uint8_t fifoBuffer[64]; // FIFO storage buffer

// orientation/motion vars
Quaternion q;           // [w, x, y, z]         quaternion container
VectorInt16 aa;         // [x, y, z]            accel sensor measurements
VectorInt16 aaReal;     // [x, y, z]            gravity-free accel sensor measurements
VectorInt16 aaWorld;    // [x, y, z]            world-frame accel sensor measurements
VectorFloat gravity;    // [x, y, z]            gravity vector
float euler[3];         // [psi, theta, phi]    Euler angle container
float ypr[3];           // [yaw, pitch, roll]   yaw/pitch/roll container and gravity vector

// packet structure for InvenSense teapot demo
uint8_t teapotPacket[14] = { '$', 0x02, 0, 0, 0, 0, 0, 0, 0, 0, 0x00, 0x00, '\r', '\n' };



// ================================================================
// ===               INTERRUPT DETECTION ROUTINE                ===
// ================================================================

volatile bool mpuInterrupt = false;     // indicates whether MPU interrupt pin has gone high
void dmpDataReady() {
  mpuInterrupt = true;
}
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

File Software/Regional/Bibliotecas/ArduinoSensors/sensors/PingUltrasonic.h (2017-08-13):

/*
	Ultrasonic.h - Library for Ping and HR-SC04 Ultrasonic Ranging Module.

	In order to use PING sensors (One wire for data only), use:
		PingUltrasonic myUltrasonic(dataPin);
	
	In order to use with two wire (Trigger and Echo) sensors, use:
		PingUltrasonic myUltrasonic(triggerPin, echoPin);


	Working range: 3 - 500

	For instructions, go to https://github.com/ivanseidel/Arduino-Sensors

	Modified by	Ivan Seidel Gomes, June, 2013.
	Released into the public domain.
*/

#ifndef Ultrasonic_h
#define Ultrasonic_h

#include <Arduino.h>

#include <Thread.h>
#include <interfaces/DistanceInterface.h>

class PingUltrasonic: public Thread, public DistanceInterface
{
private:
	int trigPin;
	int echoPin;

	long duration;
	float distance;

	void sendCommand(){
		// Set pin as output
		if(trigPin == echoPin)
			pinMode(trigPin, OUTPUT);

		// Make shure it's LOW (Erase state)
		digitalWrite(trigPin, LOW);
		delayMicroseconds(2);

		// Send pulse
		digitalWrite(trigPin, HIGH);
		delayMicroseconds(10);
		digitalWrite(trigPin, LOW);

		// Set pin as input
		if(trigPin == echoPin)
			pinMode(echoPin, INPUT);
	}

	bool waitResponse(){
		long startTime = micros();

		// Waits it to get HIGH
		while(digitalRead(echoPin) == LOW){
			if(micros() - startTime > 1000){
				return false;
				break;
			}
		}
		return true;
	}

public:
	PingUltrasonic(int _trigPin, int _echoPin = -1) : Thread(){
		trigPin = _trigPin;

		/*
			Ping sensors uses only one pin to trigger and echo
		*/
		if(echoPin < 0)
			echoPin = trigPin;
		else
			echoPin = _echoPin;

		pinMode(trigPin, OUTPUT);
		pinMode(echoPin, INPUT);

		minDistance = 3;
		maxDistance = 500;

		setInterval(50);
	}

	virtual float getDistance(){
		return distance;
	}

	virtual float readDistance(){
		// Send pulse to trigger reading action
		sendCommand();

		/*
			After reading, if this flag is true, indicates either:
				* Sensor is not connected (echo is not responding)
				* Timeout on reading pulse
		*/
		bool error = false;
		
		// Start time to compare later
		long startTime = micros();

		// Waits for the pulse, and check if returned true
		if(waitResponse()){
		
			// Reads HIGH pulse time
			while(digitalRead(echoPin) == HIGH){
				if(micros() - startTime > 50000){
					error = true;
					// Serial.println("FAIL2!");
					// Serial.print("FAIL2!\t");
					break;
				}
			}

		}else{
			error = true;
		}

		// Calculates duration
		duration = micros() - startTime;

		// If error, then doesen't update value
		if(!error)
			distance = duration / 29.0 / 2;
		else
			distance = maxDistance;

		return getDistance();
	}

	/*
		Check if the sensor is connected
	*/
	virtual bool isConnected(){
		sendCommand();
		return waitResponse();
	}

	/*
		Thread implementation
	*/
	virtual void run(){
		readDistance();

		runned();
	}

};

extern PingUltrasonic Ultrasonic;

#endif

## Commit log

2017-08-30 Limpeza da Programação e Leitura de Sensores
2017-08-31 Teste PID e retirada do RGB
2017-09-04 Exclude function read green sensors and move to read all sensors
2017-09-04 Quadrature encoder robot move
2017-09-07 Implements MPU6050 with bugs
    [Actions.h, Config.h, Controllers.h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]
2017-09-07 Fix bug in MPU6050 curves
    [Actions.h, Config.h, ProgramandoPaulo.ino]
2017-09-07 Fix final changes mpu 6050
    [Actions.h, Config.h, ProgramandoPaulo.ino]
2017-09-07 Fix encoder debug duplicated
    [Actions.h]
2017-09-07 Fix bugs in MPU6050
    [Actions.h, Controllers.h, ProgramandoPaulo.ino]
2017-09-08 Change port sensors
2017-09-08 Fix follow line bugs
    [Actions.h, Config.h, Controllers.h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]
2017-09-08 Servo default position

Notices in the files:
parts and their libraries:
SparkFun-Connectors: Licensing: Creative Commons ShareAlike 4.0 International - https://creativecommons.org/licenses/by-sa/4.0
